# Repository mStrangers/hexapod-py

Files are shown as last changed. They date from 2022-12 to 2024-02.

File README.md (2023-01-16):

#  Hexapod

A Hexapod Robot using Raspberry Pi Zero W

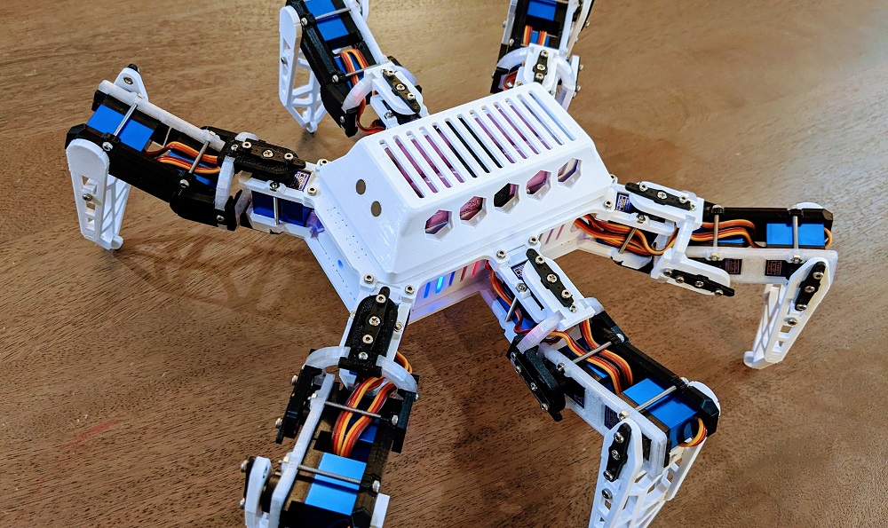
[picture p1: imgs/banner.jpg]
banner


[google_play](https://play.google.com/store/apps/details?id=com.rookiedev.hexapod)
[windows](https://github.com/rookiepeng/hexapod/releases)
[linux](https://github.com/rookiepeng/hexapod/releases)

## Introduction

This is a hexapod robot based on [Smallp Tsai](https://github.com/SmallpTsai)'s [hexapod-v2-7697](https://github.com/SmallpTsai/hexapod-v2-7697) project.
This project reused most of the mechanical design in the original project, but with a full redesign of the circuits and software.
The table below shows the difference between this project and the original one.

| | Original hexapod-v2-7697 | This project |
| --- | --- | --- |
| Controller | Linkit 7697 | Raspberry Pi Zero W or Raspberry Pi Zero W 2 |
| PWM control | Custom circuit board | 2 x PCA9685 motor driver boards |
| DC-DC | 7 x mini360 modules | 2 x XL4005 5A Max DC-DC modules and 1 x mini360 |
| Power | 2S Lipo battery | 2 x 18650 batteries |
| Remote | BLE | WiFi, Bluetooth |
| Remote software | Android and iOS | PC, Android |

https://user-images.githubusercontent.com/471808/148647807-02e3e901-6181-4473-8ac4-3b5998fa8d17.mp4

https://user-images.githubusercontent.com/471808/158099495-1caeb903-a2e6-4e8d-9f13-54728d7d255a.mp4

## Software

### Raspberry Pi

#### Requirements

Raspberry Pi is running [`Raspberry Pi OS`](https://www.raspberrypi.com/software/).

- Enable `I2C` through `raspi-config`

``` bash
sudo raspi-config
```

- Install required packages

``` bash
sudo apt-get install python3-numpy python3-pip
```

- Install required Python modules

``` bash
pip3 install adafruit-circuitpython-servokit
```

> Tips: It is convenient to debug code on Raspberry Pi through VSCode's remote feature.

#### Running

The hexapod program, located under `./software/raspberry pi/`, is written in Python. Use the following command to start it manually.

``` bash
python3 hexapod.py
```

### Android

screenshot_wifi screenshot_bluetooth

screenshot_control1

screenshot_control2

### PC

PC program source files are located under `./software/pc/`. The compiled program can be downloaded under the [release](https://github.com/rookiepeng/hexapod/releases) page.

pc_interface

- Find the correct IP address of the Raspberry Pi on the hexapod
- Connect to the hexapod using the IP address
- Use the buttons on the panel to control the hexapod

## Mechanism

### Bill of Materials (BOM)

#### Servos

18 TowerPro [MG92B](http://www.towerpro.com.tw/product/mg92b/) are required.

> The dimension of 3d printed part is highly dependent on the servo's size. Modification is required if you want to use alternative servos.

#### 3D-Printed Parts

##### Body x 1

| Filename | Thumbnail | Required |
| --- | --- | --- |
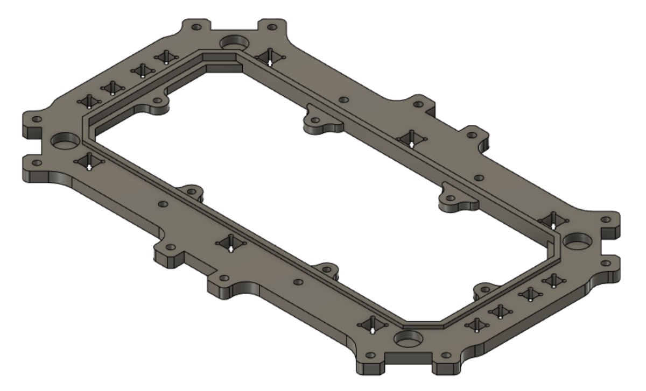
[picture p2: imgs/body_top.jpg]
body_top
| body_top |  | 1 |
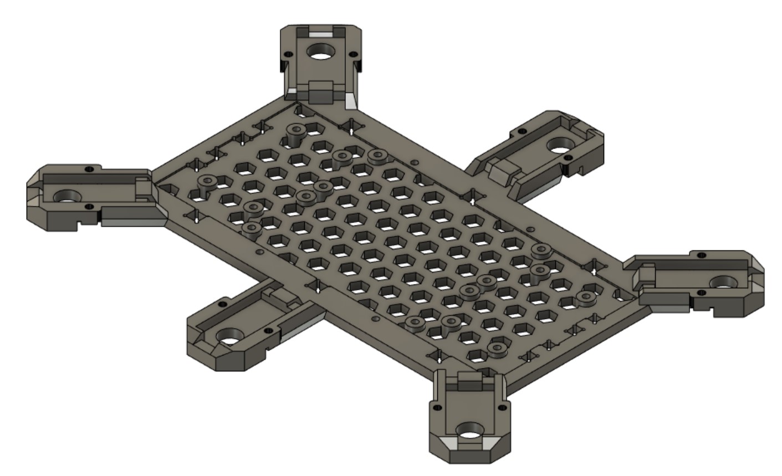
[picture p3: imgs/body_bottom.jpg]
body_bottom
| body_bottom |  | 1 |
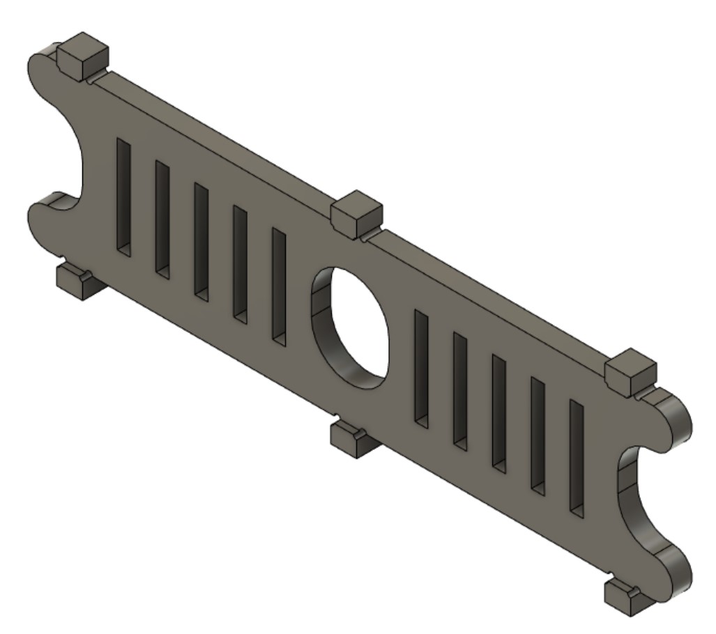
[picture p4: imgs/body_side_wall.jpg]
body_side_wall
| body_side_wall |  | 2 |
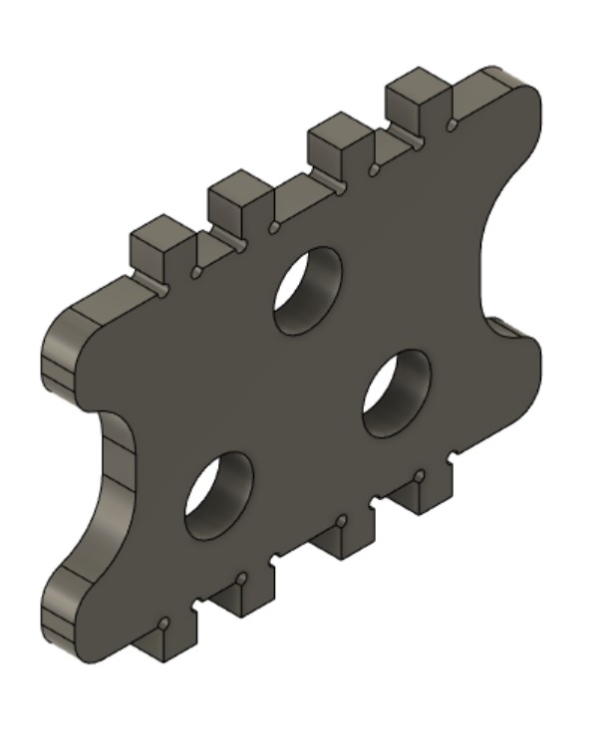
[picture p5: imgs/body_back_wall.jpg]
body_back_wall
| body_back_wall |  | 2 |
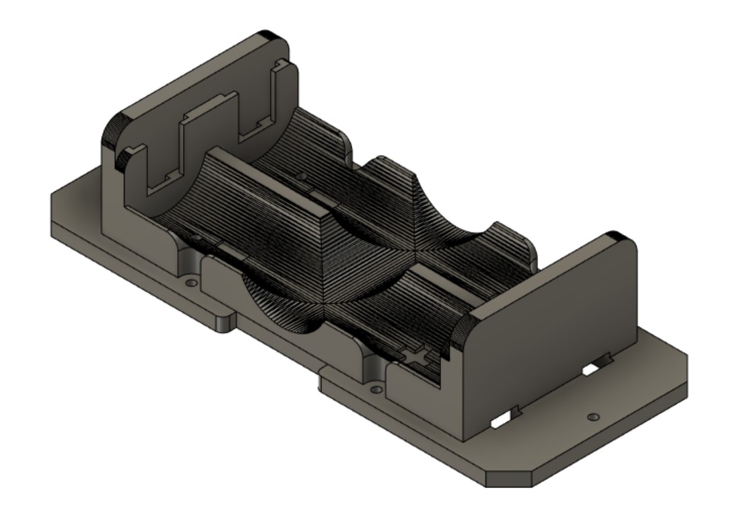
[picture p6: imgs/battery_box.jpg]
battery_box
| battery_box |  | 1 |
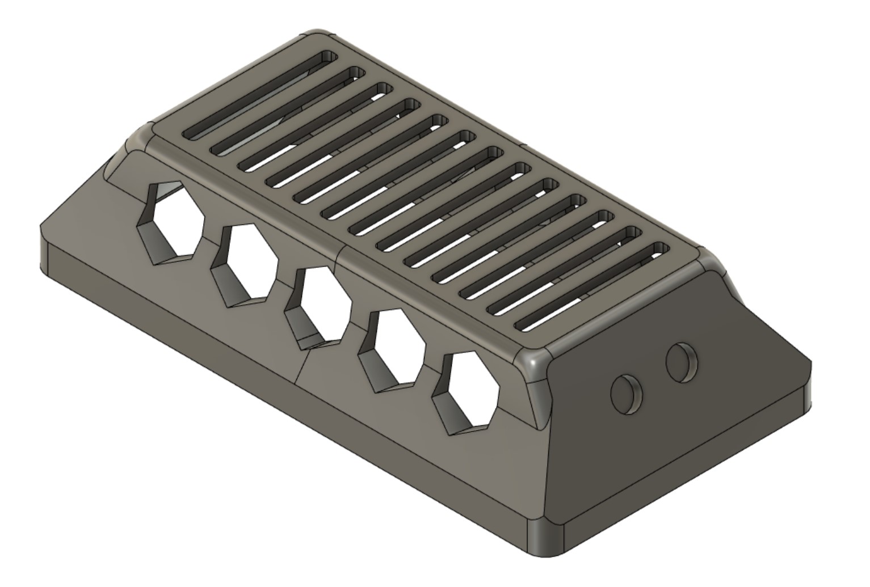
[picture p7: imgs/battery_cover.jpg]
battery_cover
| battery_cover  |  | 1 |

##### Leg x 6

| Filename | Thumbnail | Required |
| --- | --- | --- |
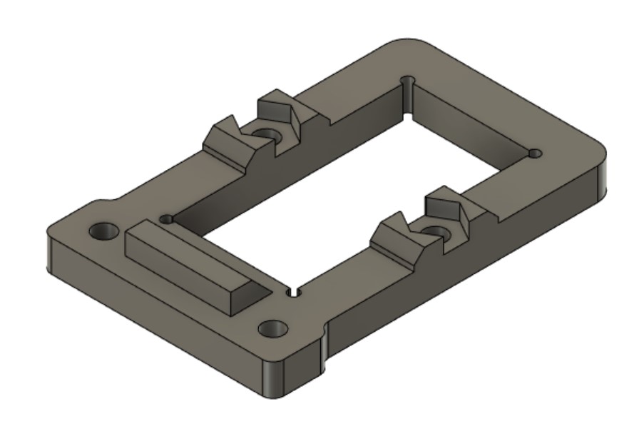
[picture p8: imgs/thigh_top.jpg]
thigh_top
| thigh_top |  | 1 (x6) |
| joint_cross | joint_cross | 1 (x6) |
| joint_top | joint_top | 2 (x6) |
| joint_bottom | joint_bottom | 2 (x6) |
| leg_top | leg_top | 1 (x6) |
| let_bottom | leg_bottom | 1 (x6) |
| foot_top | foot_top | 1 (x6) |
| foot_bottom | foot_bottom | 1 (x6) |
| foot_ground | foot_ground | 1 (x6) |
| foot_tip | foot_tip | 1 (x6) |

#### Others

| Name | Spec | Thumbnail | Required | Note |
| --- | --- | --- | --- | --- |
| Screw | M2 6mm  | 6mm | 54 | Servo Arm: 1 x 18<br>Joint: 4 x 6<br>Thigh: 2 x 6 |
| Screw | M2 10mm | 10mm | 24 | Thigh: 1 x 6<br>Pin lock: 1 x 18 |
| Screw | M2 30mm | 30mm | 36 | Servo: 2 x 18 |
| Nuts | M2 | 6mm | 36 | Servo: 2 x 18 |
| Pin (304) | M4 6mm  | pin | 18 | Servo: 1 x 18 |

### Leg Assemble

#### Assembly video



#### Exploded view

LegAssemble

#### Detailed steps

- **Step 1** - Combine `thigh_top`, `MG92B` and `thigh_bottom`, use M2x30mm screw and nut to secure them together.

LegAssemble1

- **Step 2** - Grab one `joint_cross`, `joint_top` and `joint_bottom` and combine them

LegAssemble2

- **Step 3** - First put 2 x `MG92B`, `leg_top` and `leg_bottom` together with M2x30mm screw and nut. Then attach `joint_top` and `joint_bottom` altogether

LegAssemble3

- **Step 4** - Grab `foot_top`, `foot_bottom` and `foot_ground` (and `foot_top`) and assemble them.

LegAssemble4

- **Finish** - Great, you got 1 leg done, 5 more to go :)

LegAssemble5

## Electronics

### Bill of Materials (BOM)

| Name | Thumbnail | Required |
| --- | --- | --- |
| Raspberry Pi Zero W or W 2 | raspberry pi | 1 |
| PCA9685 motor driver | PCA9685 | 2 |
| XL4005 DC-DC step down | XL4005 | 2 |
| Mini 360 DC-DC step down | mini360 | 1 |
| Toggle switch | toggle_switch  | 1 |

### Connection Diagram

diagram

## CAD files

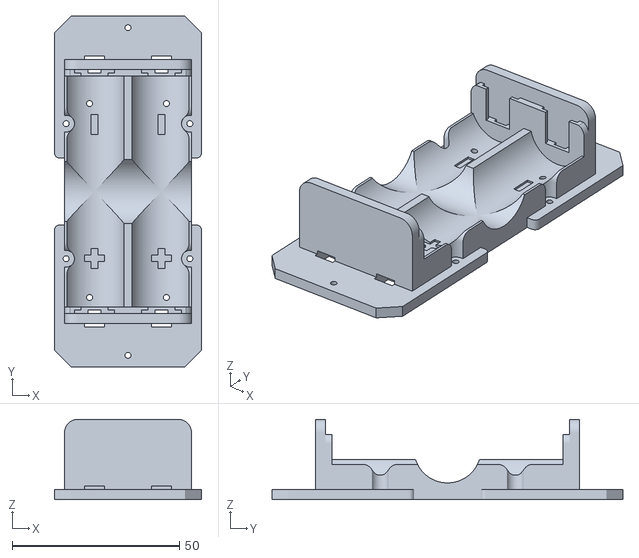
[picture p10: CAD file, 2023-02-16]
mechanism/battery_box.stl
44.0 x 105.0 x 24.0

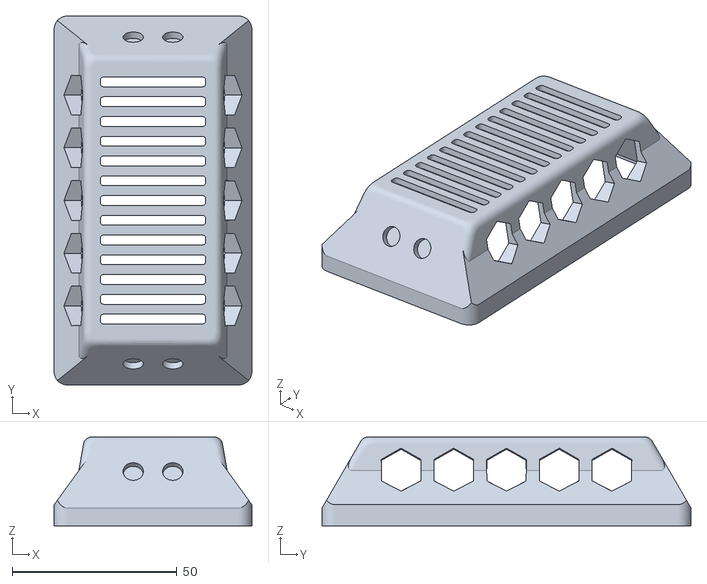
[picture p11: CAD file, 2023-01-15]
mechanism/cover.stl
60.0 x 112.0 x 27.0

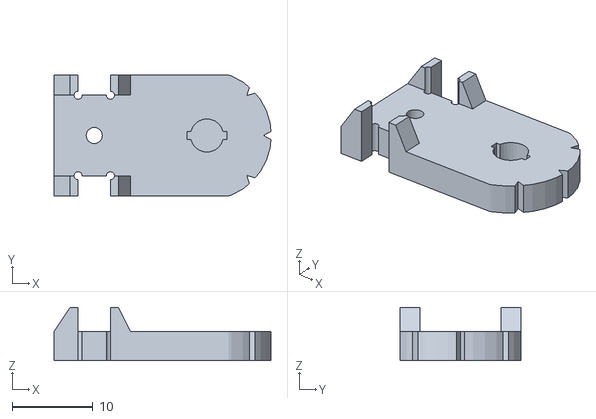
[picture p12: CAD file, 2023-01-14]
mechanism/joint_bottom.stl
27.0 x 15.0 x 6.60

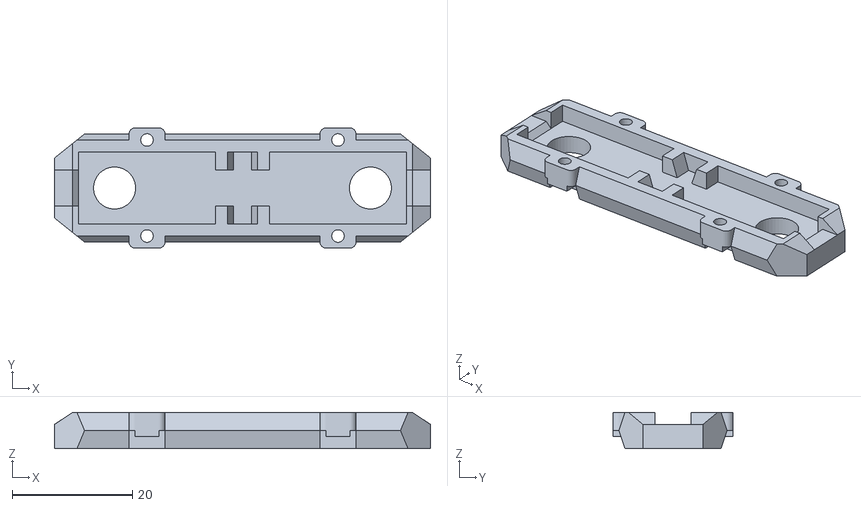
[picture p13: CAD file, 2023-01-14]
mechanism/leg_bottom.stl
62.6 x 20.0 x 6.00

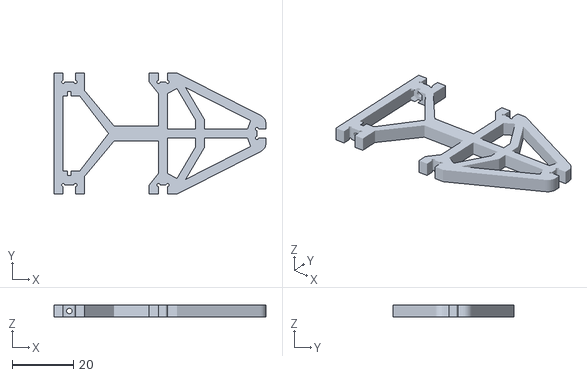
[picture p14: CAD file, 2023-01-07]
mechanism/foot_ground.stl
69.0 x 39.5 x 4.00

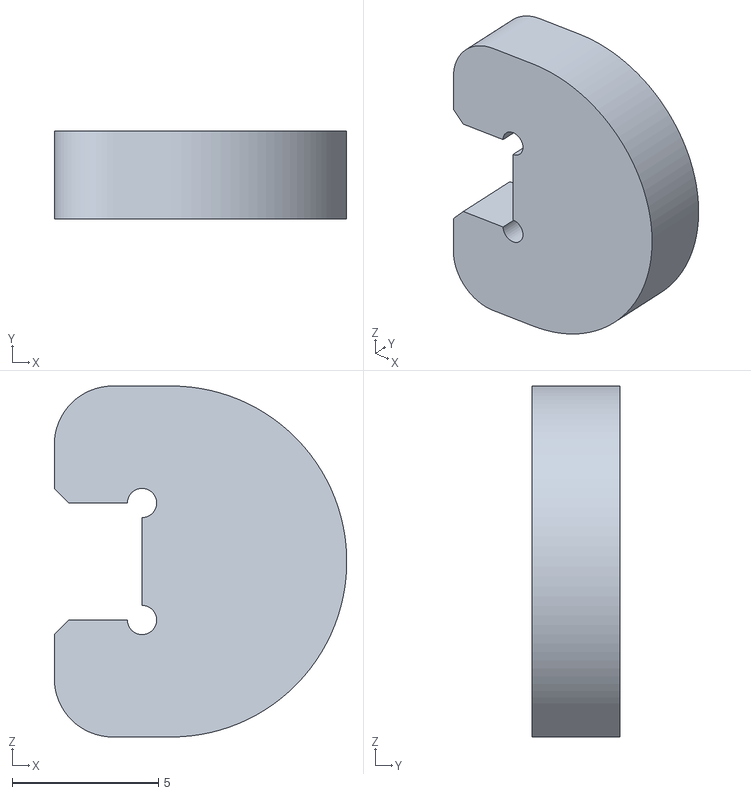
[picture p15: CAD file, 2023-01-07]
mechanism/foot_tip.stl
10.00 x 3.00 x 12.0

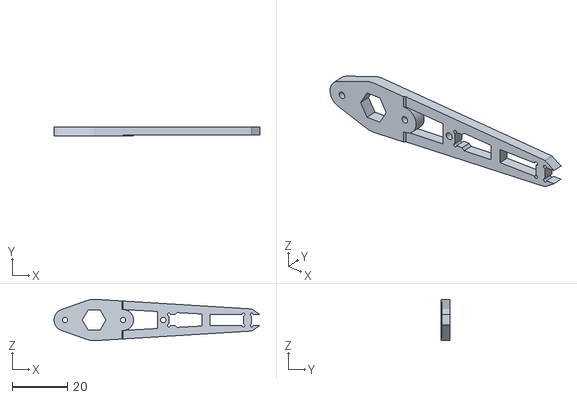
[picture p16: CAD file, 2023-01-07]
mechanism/foot_top.stl
74.5 x 3.40 x 15.0

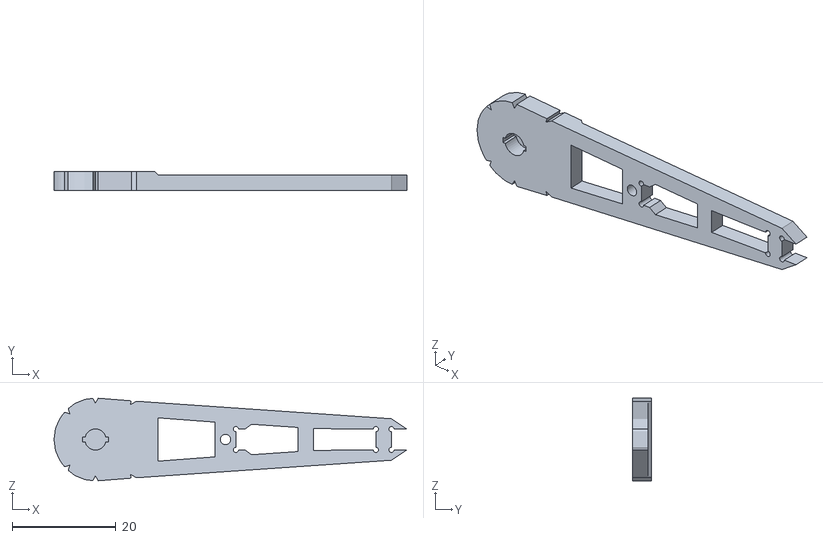
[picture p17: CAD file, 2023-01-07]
mechanism/foot_bottom.stl
68.1 x 3.60 x 15.9

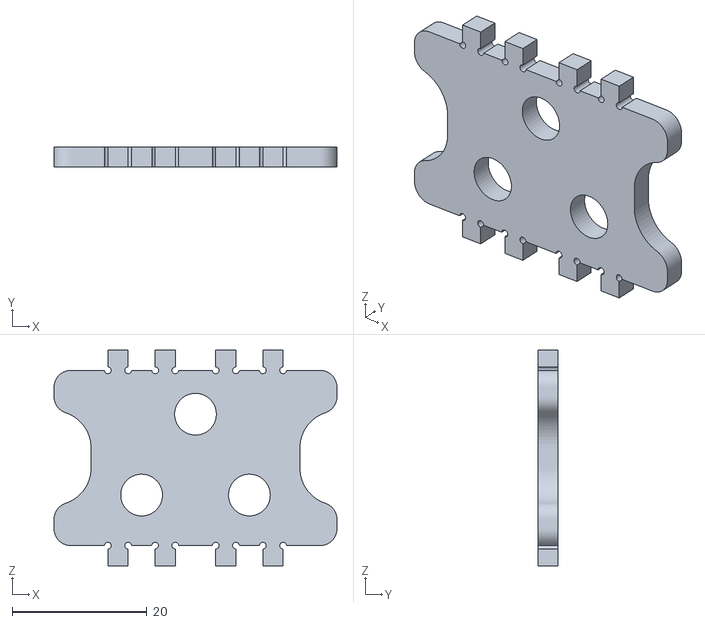
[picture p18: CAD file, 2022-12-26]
mechanism/front_back_wall_tall.stl
42.0 x 3.00 x 32.0

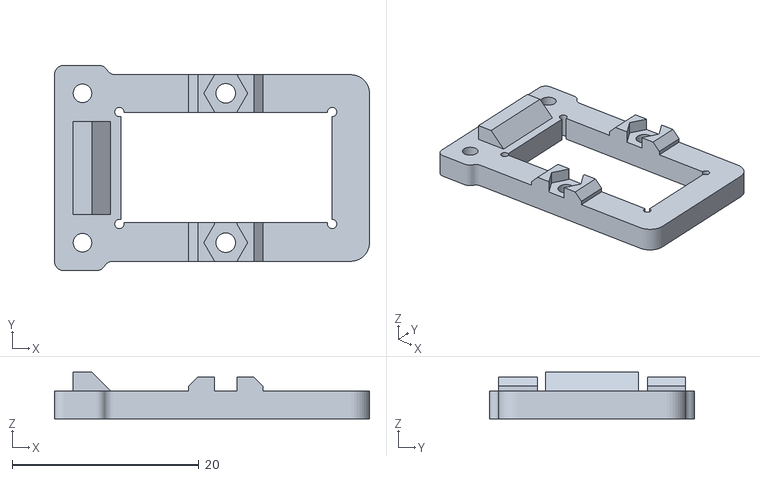
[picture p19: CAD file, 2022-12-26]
mechanism/thigh_top.stl
33.8 x 22.0 x 5.00

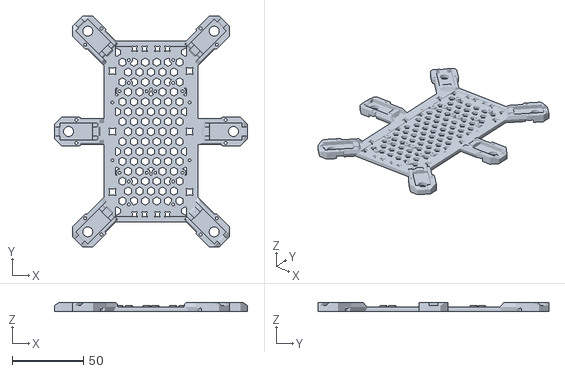
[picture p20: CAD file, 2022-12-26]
mechanism/base.stl
135.3 x 161.6 x 6.00

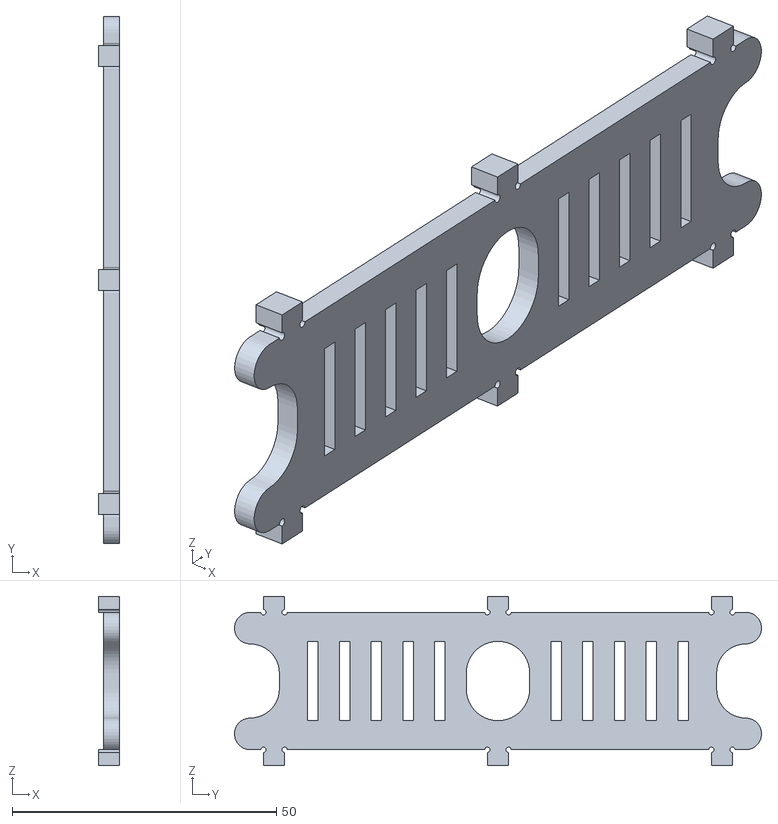
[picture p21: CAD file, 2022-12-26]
mechanism/side_tall.stl
4.00 x 99.7 x 32.0

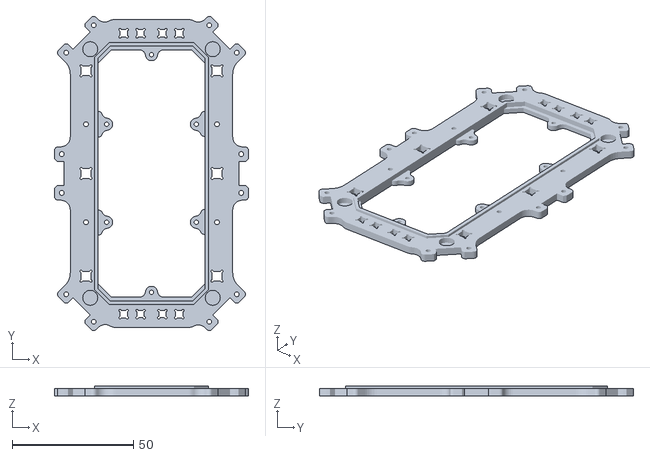
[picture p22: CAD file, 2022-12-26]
mechanism/top_new.stl
80.0 x 129.6 x 4.00

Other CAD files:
mechanism/Fusion360/hexapod.f3d
mechanism/Fusion360/joystick.f3d

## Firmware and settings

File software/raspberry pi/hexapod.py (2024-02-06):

#!python
#
# 2021 - PRESENT  Zhengyu Peng
# Website: https://zpeng.me
#
# `                      `
# -:.                  -#:
# -//:.              -###:
# -////:.          -#####:
# -/:.://:.      -###++##:
# ..   `://:-  -###+. :##:
#        `:/+####+.   :##:
# .::::::::/+###.     :##:
# .////-----+##:    `:###:
#  `-//:.   :##:  `:###/.
#    `-//:. :##:`:###/.
#      `-//:+######/.
#        `-/+####/.
#          `+##+.
#           :##:
#           :##:
#           :##:
#           :##:
#           :##:
#            .+:

# Libraries
# https://circuitpython.readthedocs.io/projects/servokit/en/latest/
from audioop import reverse
#from adafruit_servokit import ServoKit
from ssc32 import SSC32

from leg import Leg

from queue import Queue, Empty

# python3-numpy
import numpy as np
import time
import json
from path_generator import gen_walk_path
from path_generator import gen_fastwalk_path
from path_generator import gen_turn_path
# from path_generator import gen_shift_path
from path_generator import gen_climb_path
from path_generator import gen_rotatex_path, gen_rotatey_path, gen_rotatez_path
from path_generator import gen_twist_path

from threading import Thread

from tcpserver import TCPServer
from btserver import BluetoothServer


class Hexapod(Thread):
    CMD_STANDBY = 'standby'
    CMD_LAYDOWN = 'laydown'

    CMD_WALK_0 = 'walk0'
    CMD_WALK_180 = 'walk180'

    CMD_WALK_R45 = 'walkr45'
    CMD_WALK_R90 = 'walkr90'
    CMD_WALK_R135 = 'walkr135'

    CMD_WALK_L45 = 'walkl45'
    CMD_WALK_L90 = 'walkl90'
    CMD_WALK_L135 = 'walkl135'

    CMD_FASTFORWARD = 'fastforward'
    CMD_FASTBACKWARD = 'fastbackward'

    CMD_TURNLEFT = 'turnleft'
    CMD_TURNRIGHT = 'turnright'

    CMD_CLIMBFORWARD = 'climbforward'
    CMD_CLIMBBACKWARD = 'climbbackward'

    CMD_ROTATEX = 'rotatex'
    CMD_ROTATEY = 'rotatey'
    CMD_ROTATEZ = 'rotatez'

    CMD_TWIST = 'twist'

    CMD_CALIBRATION = 'calibration'
    CMD_NORMAL = 'normal'

    def __init__(self, in_cmd_queue):
        Thread.__init__(self)

        self.cmd_queue = in_cmd_queue
        self.interval = 0.005

        self.calibration_mode = False

        with open('/home/mikael/hexapod-py/software/raspberry pi/config.json', 'r') as read_file:
            self.config = json.load(read_file)

        # legs' coordinates
        # x -> right
        # y -> front
        # z -> up
        # origin is the center of the body
        # roots are the positions of the bottom screws
        # length units are in mm
        # time units are in ms
        self.mount_x = np.array(self.config['legMountX'])
        self.mount_y = np.array(self.config['legMountY'])
        self.root_j1 = self.config['legRootToJoint1']
        self.j1_j2 = self.config['legJoint1ToJoint2']
        self.j2_j3 = self.config['legJoint2ToJoint3']
        self.j3_tip = self.config['legJoint3ToTip']
        self.mount_angle = np.array(self.config['legMountAngle'])/180*np.pi
        self.mount_position = np.zeros((6, 3))
        self.mount_position[:, 0] = self.mount_x
        self.mount_position[:, 1] = self.mount_y

        # Objects
        #self.pca_left = ServoKit(channels=16, address=0x40, frequency=50)
        #self.pca_right = ServoKit(channels=16, address=0x41, frequency=50)
        self.ssc = SSC32('/dev/ttyACM0', 115200,count=18, autocommit=1000)
        self.legs = [
            # front right
            Leg(0,
                [self.ssc[0], self.ssc[1],
                 self.ssc[2]],
                correction=self.config.get('leg0Offset', [0, 0, 0])),
            # center right
            Leg(1,
                [self.ssc[3], self.ssc[4],
                 self.ssc[5]],
                correction=self.config.get('leg1Offset', [0, 0, 0])),
            # rear right
            Leg(2,
                [self.ssc[6], self.ssc[7],
                 self.ssc[8]],
                correction=self.config.get('leg2Offset', [0, 0, 0])),
            # rear left
            Leg(3,
                [self.ssc[9], self.ssc[10],
                 self.ssc[11]],
                correction=self.config.get('leg3Offset', [0, 0, 0])),
            # center left
            Leg(4,
                [self.ssc[12], self.ssc[13],
                 self.ssc[14]],
                correction=self.config.get('leg4Offset', [0, 0, 0])),
            # front left
            Leg(5,
                [self.ssc[15], self.ssc[16],
                 self.ssc[17]],
                correction=self.config.get('leg5Offset', [0, 0, 0]))]

        # self.leg_0.reset(True)
        # self.leg_1.reset(True)
        # self.leg_2.reset(True)
        # self.leg_3.reset(True)
        # self.leg_4.reset(True)
        # self.leg_5.reset(True)

        #self.standby_posture = self.gen_posture(60, 75)
        self.standby_posture = self.gen_posture(self.config.get('standbyPostureJ2', 60), self.config.get('standbyPostureJ3', 75))

        self.current_motion = self.standby_posture

        self.cmd_dict = {
            self.CMD_STANDBY: self.standby_posture,
            self.CMD_LAYDOWN: self.gen_posture(self.config.get('laydownPostureJ2', 0), self.config.get('laydownPostureJ3', 15)),
            self.CMD_WALK_0: gen_walk_path(
                self.standby_posture['coord'], direction=0),
            self.CMD_WALK_180: gen_walk_path(
                self.standby_posture['coord'], direction=180),
            self.CMD_WALK_R45: gen_walk_path(
                self.standby_posture['coord'], direction=315),
            self.CMD_WALK_R90: gen_walk_path(
                self.standby_posture['coord'], direction=270),
            self.CMD_WALK_R135: gen_walk_path(
                self.standby_posture['coord'], direction=225),
            self.CMD_WALK_L45: gen_walk_path(
                self.standby_posture['coord'], direction=45),
            self.CMD_WALK_L90: gen_walk_path(
                self.standby_posture['coord'], direction=90),
            self.CMD_WALK_L135: gen_walk_path(
                self.standby_posture['coord'], direction=135),
            self.CMD_FASTFORWARD: gen_fastwalk_path(
                self.standby_posture['coord']),
            self.CMD_FASTBACKWARD: gen_fastwalk_path(
                self.standby_posture['coord'], reverse=True),
            self.CMD_TURNLEFT: gen_turn_path(
                self.standby_posture['coord'], direction='left'),
            self.CMD_TURNRIGHT: gen_turn_path(
                self.standby_posture['coord'], direction='right'),
            self.CMD_CLIMBFORWARD: gen_climb_path(
                self.standby_posture['coord'], reverse=False),
            self.CMD_CLIMBBACKWARD: gen_climb_path(
                self.standby_posture['coord'], reverse=True),
            self.CMD_ROTATEX: gen_rotatex_path(self.standby_posture['coord']),
            self.CMD_ROTATEY: gen_rotatey_path(self.standby_posture['coord']),
            self.CMD_ROTATEZ: gen_rotatez_path(self.standby_posture['coord']),
            self.CMD_TWIST: gen_twist_path(self.standby_posture['coord'])
        }

        self.posture(self.standby_posture['coord'])
        time.sleep(1)

    def gen_posture(self, j2_angle, j3_angle):
        j2_rad = j2_angle/180*np.pi
        j3_rad = j3_angle/180*np.pi
        posture = np.zeros((6, 3))

        posture[:, 0] = self.mount_x+(self.root_j1+self.j1_j2+(
            self.j2_j3*np.sin(j2_rad))+self.j3_tip*np.cos(j3_rad)) *\
            np.cos(self.mount_angle)
        posture[:, 1] = self.mount_y + (self.root_j1+self.j1_j2+(
            self.j2_j3*np.sin(j2_rad))+self.j3_tip*np.cos(j3_rad)) *\
            np.sin(self.mount_angle)
        posture[:, 2] = self.j2_j3 * \
            np.cos(j2_rad) - self.j3_tip * \
            np.sin(j3_rad)
        return {'coord': posture,
                'type': 'posture'}

    def posture(self, coordinate):
        angles = self.inverse_kinematics(coordinate)

        self.legs[0].move_junctions(angles[0, :])
        self.legs[5].move_junctions(angles[5, :])

        self.legs[1].move_junctions(angles[1, :])
        self.legs[4].move_junctions(angles[4, :])

        self.legs[2].move_junctions(angles[2, :])
        self.legs[3].move_junctions(angles[3, :])

    def move(self, path):
        for p_idx in range(0, np.shape(path)[0]):
            dest = path[p_idx, :, :]
            angles = self.inverse_kinematics(dest)

            self.legs[0].move_junctions(angles[0, :])
            self.legs[5].move_junctions(angles[5, :])

            self.legs[1].move_junctions(angles[1, :])
            self.legs[4].move_junctions(angles[4, :])

            self.legs[2].move_junctions(angles[2, :])
            self.legs[3].move_junctions(angles[3, :])

            # time.sleep(self.interval)

    def motion(self, path):
        for p_idx in range(0, np.shape(path)[0]):
            dest = path[p_idx, :, :]
            angles = self.inverse_kinematics(dest)

            self.legs[0].move_junctions(angles[0, :])
            self.legs[5].move_junctions(angles[5, :])

            self.legs[1].move_junctions(angles[1, :])
            self.legs[4].move_junctions(angles[4, :])

            self.legs[2].move_junctions(angles[2, :])
            self.legs[3].move_junctions(angles[3, :])

            try:
                cmd_string = self.cmd_queue.get(block=False)
                print('interrput')
            except Empty:
                # time.sleep(self.interval)
                pass
            else:
                self.cmd_handler(cmd_string)
                break

    def inverse_kinematics(self, dest):
        temp_dest = dest-self.mount_position
        local_dest = np.zeros_like(dest)
        local_dest[:, 0] = temp_dest[:, 0] * \
            np.cos(self.mount_angle) + \
            temp_dest[:, 1] * np.sin(self.mount_angle)
        local_dest[:, 1] = temp_dest[:, 0] * \
            np.sin(self.mount_angle) - \
            temp_dest[:, 1] * np.cos(self.mount_angle)
        local_dest[:, 2] = temp_dest[:, 2]

        angles = np.zeros((6, 3))
        x = local_dest[:, 0] - self.root_j1
        y = local_dest[:, 1]

        angles[:, 0] = -(np.arctan2(y, x) * 180 / np.pi)+90

        x = np.sqrt(x*x + y*y) - self.j1_j2
        y = local_dest[:, 2]
        ar = np.arctan2(y, x)
        lr2 = x*x + y*y
        lr = np.sqrt(lr2)
        a1 = np.arccos((lr2 + self.j2_j3*self.j2_j3 -
                        self.j3_tip*self.j3_tip)/(2*self.j2_j3*lr))
        a2 = np.arccos((lr2 - self.j2_j3*self.j2_j3 +
                        self.j3_tip*self.j3_tip)/(2*self.j3_tip*lr))

        angles[:, 1] = 90-((ar + a1) * 180 / np.pi)
        angles[:, 2] = (90 - ((a1 + a2) * 180 / np.pi))+90

        return angles

    def cmd_handler(self, cmd_string):
        data = cmd_string.split(':')[-2]

        if data == self.CMD_CALIBRATION:
            self.calibration_mode = True
            self.legs[0].reset(calibrated=True)
            self.legs[1].reset(calibrated=True)
            self.legs[2].reset(calibrated=True)
            self.legs[3].reset(calibrated=True)
            self.legs[4].reset(calibrated=True)
            self.legs[5].reset(calibrated=True)
        elif data == self.CMD_NORMAL:
            self.calibration_mode = False
        else:
            if self.calibration_mode:
                self.calibration_cmd_handler(data)
            else:
                self.current_motion = self.cmd_dict.get(
                    data, self.standby_posture)

        self.cmd_queue.task_done()

    def calibration_cmd_handler(self, cmd_string):
        data_array = cmd_string.split(',')
        if len(data_array) == 4:
            op = data_array[0].lstrip()

            leg_idx = int(data_array[1])
            if leg_idx < 0 or leg_idx > 5:
                return

            joint_idx = int(data_array[2])
            if joint_idx < 0 or joint_idx > 2:
                return

            angle = float(data_array[3])
            if op == 'angle':
                self.legs[leg_idx].set_angle(joint_idx, angle)
            elif op == 'offset':
                self.legs[leg_idx].correction[joint_idx] = angle
                self.legs[leg_idx].reset(calibrated=True)

                config_str = 'leg'+str(leg_idx)+'Offset'
                self.config[config_str] = self.legs[leg_idx].correction
                self.save_config()

    def save_config(self):
        try:
            json.dump(self.config, open(
                '/home/mikael/hexapod-py/software/raspberry pi/config.json', 'w+'), indent=4)
        except PermissionError as err:
            pass

    def run(self):
        while True:
            # if self.current_motion is None:
            try:
                cmd_string = self.cmd_queue.get(block=False)
            except Empty:
                # time.sleep(self.interval)
                pass
            else:
                self.cmd_handler(cmd_string)

            if not self.calibration_mode:
                if self.current_motion['type'] == 'motion':
                    self.motion(self.current_motion['coord'])
                elif self.current_motion['type'] == 'posture':
                    self.posture(self.current_motion['coord'])


def main():
    q = Queue()
    tcp_server = TCPServer(q)
    tcp_server.start()

    #bt_server = BluetoothServer(q)
    #bt_server.start()

    hexapod = Hexapod(q)
    hexapod.start()


if __name__ == '__main__':
    main()

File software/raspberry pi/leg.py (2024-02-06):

#!python
#
# 2021  Zhengyu Peng
# Website: https://zpeng.me
#
# `                      `
# -:.                  -#:
# -//:.              -###:
# -////:.          -#####:
# -/:.://:.      -###++##:
# ..   `://:-  -###+. :##:
#        `:/+####+.   :##:
# .::::::::/+###.     :##:
# .////-----+##:    `:###:
#  `-//:.   :##:  `:###/.
#    `-//:. :##:`:###/.
#      `-//:+######/.
#        `-/+####/.
#          `+##+.
#           :##:
#           :##:
#           :##:
#           :##:
#           :##:
#            .+:

import numpy as np


class Leg:
    def __init__(self,
                 id,
                 junction_servos,
                 correction=[0, 0, 0],
                 scale=[1, 1, 1],
                 constraint=[[35, 145], [0, 165], [30, 150]]):
        self.id = id
        self.junction_servos = junction_servos
        self.correction = correction
        self.constraint = constraint

    def set_angle(self, junction, angle):
        set_angle = np.min(
            [angle+self.correction[junction], self.constraint[junction][1]+self.correction[junction], 180])
        set_angle = np.max(
            [set_angle, self.constraint[junction][0]+self.correction[junction], 0])
        self.junction_servos[junction].degrees = set_angle

    def set_raw_angle(self, junction, angle):
        self.junction_servos[junction].degrees = angle

    def move_junctions(self, angles):
        self.set_angle(0, angles[0])
        self.set_angle(1, angles[1])
        self.set_angle(2, angles[2])

    def reset(self, calibrated=False):
        if calibrated:
            self.set_angle(0, 90)
            self.set_angle(1, 90)
            self.set_angle(2, 90)
        else:
            self.set_raw_angle(0, 90)
            self.set_raw_angle(1, 90)
            self.set_raw_angle(2, 90)

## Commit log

2022-11-20 swap left and right
    [hexapod.py]
2022-12-26 update design
    [base.stl, front_back_wall_tall.stl, side_tall.stl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]
2023-01-07 update design of foot
    [foot_bottom.stl, foot_ground.stl, foot_tip.stl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]
2023-01-14 update design for leg
    [joint_bottom.stl, joint_top.f3d, leg.f3d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]
2023-03-28 combine designs
    [body.f3d, foot.f3d, hexapod.f3d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]
